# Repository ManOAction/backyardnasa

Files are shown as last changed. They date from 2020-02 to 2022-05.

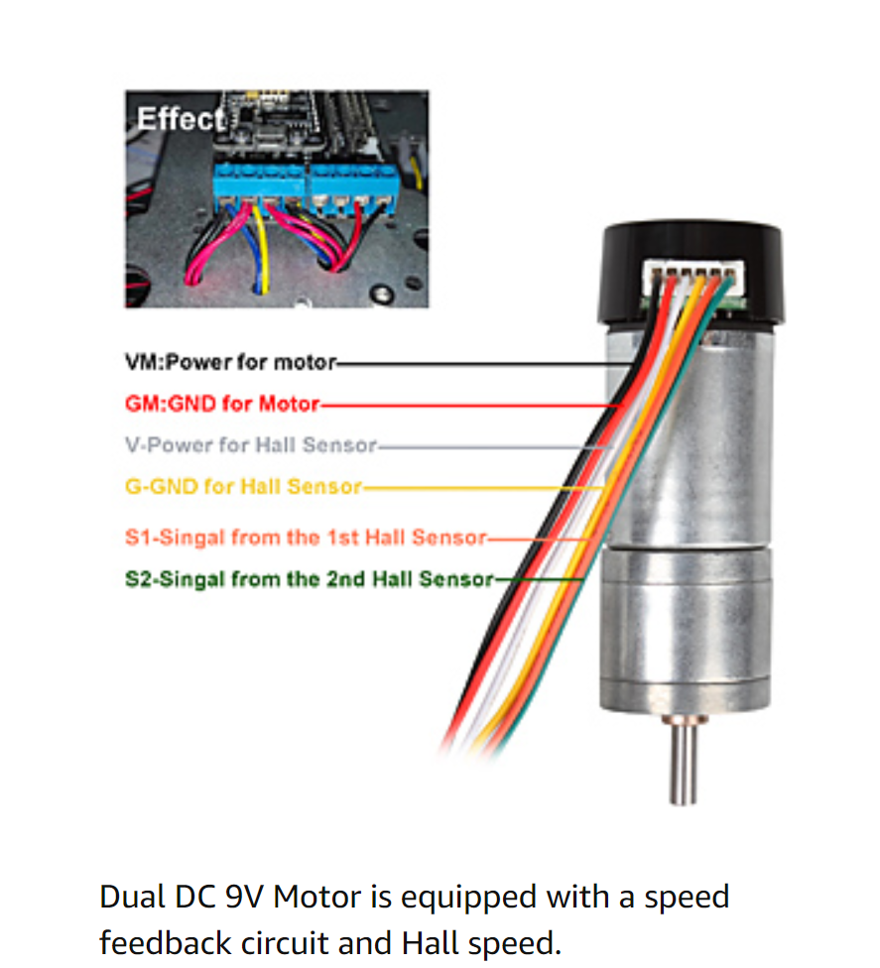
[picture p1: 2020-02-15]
docs/ChassisV2_Motor_WiringDiagram.PNG

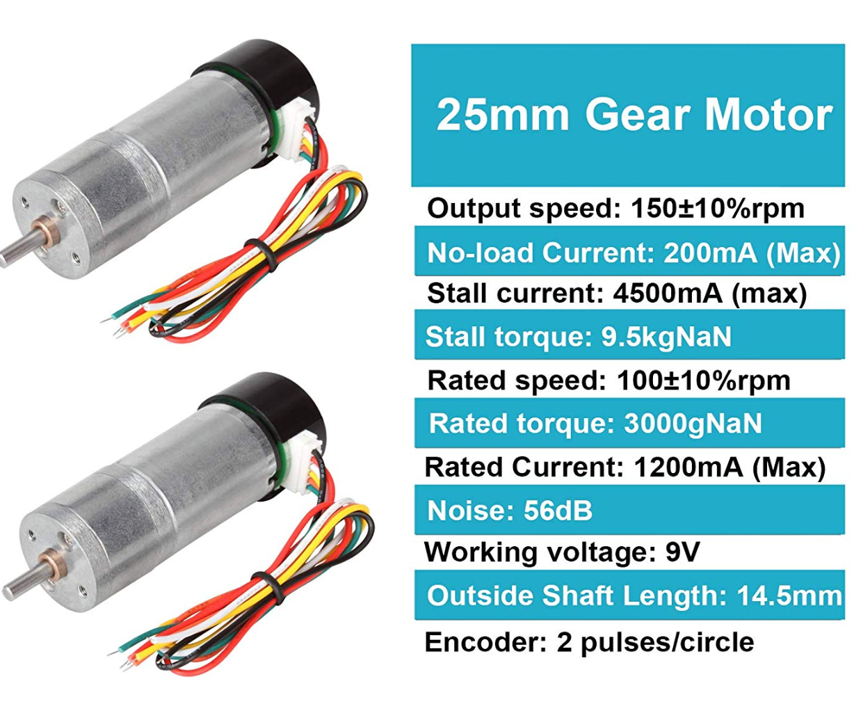
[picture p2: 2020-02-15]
docs/ChassisV2_MotorSpecs.PNG

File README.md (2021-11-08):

# Backyard NASA Rover Project
I figured making a robot rover that lived on its own somewhere and sent pictures of
rocks back to me couldn't be that hard if the gubberment folks at NASA could do it.

Her name is Matilda, and this is her story.

We started using this tutorial.
https://projects.raspberrypi.org/en/projects/physical-computing/3

New Documentation is being implemented here in Notion:
https://www.notion.so/Matilda-4c2012eff4d847c4a76360bea5a4a66a

# ChangeLog
2021-10-29, JDL -- Oh man, it's been a long time.  Moving docs to Notion and learning ROS
2020-12-27, JDL -- Updating diary and writing new roadmap for 2021
2020-07-26, JDL -- Motors, Atmo, Sonic, and Magna systems are all working.
2020-07-25, JDL -- Starting it up again.  Stuff's broke.
2020-02-22, JDL -- Rover Patterns, Temp Sensors, and Chat Capabilities
2019-11-18, JDL -- First Draft

# TODO
  Now being tracked in the "Current Roadmap Section"

# Other Ideas
Automatic Hard Iron Offset Recalibration: Use the magnet calibrator logic in the middle of
    360 turning to reset and reassign offset variables.

# Changes from Stock Raspian Setup
############################################################

We're reconfiguring the Pi to enable I2C and adding it to the kernal.
https://www.instructables.com/id/Raspberry-Pi-I2C-Python/
Note: When it says "i2cdetect -y 0" you need to say "i2c detect -y 1"

We're using an ancient library with docs listed here. (got to be something better)
http://wiki.erazor-zone.de/wiki:linux:python:smbus:doc

Following this to enable the SPI bus.
https://tutorials-raspberrypi.com/infrared-distance-measurement-with-the-raspberry-pi-sharp-gp2y0a02yk0f/

# Misc Thoughts
###########################################################

Check Bot Secrets for API info related to Chatbots

Use i2cdetect -y 1 to confirm I2C connections

Current board is loaded up on a Pi B+
pi@192.168.122.195 was the last known location
-u pi -p raspberry

##########################################################

# Broad Roadmap
##########################################################

Phase I: Basic Capabilities:
  - Pictures of Objects
  - Geofencing
  - Talking to Slack Channel  
  - Passive Charging and Voltage Checking

Phase II: Initial Backyard Trials
  - Success after multiple days of continuous operation achieved

Phase III: Scale to Pasture Size
  - Build to "coffee table" size

Phase IV: Profit?

# Current Roadmap (Newly drafted on 12/27)
##########################################################

Separate Motor Power Supply
  - This means having the computer run on a self contained system away from the
  drive motors.

  - Twin Sonic Sensors (HCSR04) for the left and right bumpers.

  - Functioning camera module that talks to a social account (slack?)

  - Update 3D printed housing for sensors, Pi, and batteries.

  - Capable of autonomous functioning until batteries deplete themselves.

# Diary
##########################################################

12/27, JDL - After lying dormant for months, matilda boots and runs fine, but the motors and power issue
  remain an issue.   I'm going to pursue using a NiMH battery to power the motors with a MOSFET in between
  to turn the battery on and off.  It looks like charging NiMH is a bit of a pain, but we're going to move
  forward with it since it's what we've got.   Passive charging/recharging may be a feature that is a long
  ways down the road.  We may as well get it to function long enough to deplete it's batteries before we try
  to learn how to recharge it.

7/26, JDL - I got tripped up on BCM/DPI pin numbering and it took a long time to fix.  Everything's working
  right now.  I'm going to clean up the codebase and then move on to a new feature to add.

7/26, JDL - This is dumb.  After looking at the official CircuitPython libraries for the HCSR04, they
  just have a poor feature set compared to this guy's custom one.  https://github.com/MarkAHeywood/Bluetin_Python_Echo
  I'm switching back to using it.

7/25, JDL - Starting back into it, and stuff's broke as we were mixed up between the Blinka library
  from Adafruit and the old stuff we had.  Frustrated because it was working until I patched a change.
  Locomotion is the only thing working and it only works at low voltage (<5V).  I need to find if I
  can use capacitors or something else to prevent the battery from shorting anytime I want more
  voltage from it.  Trying to start piece by piece putting things back online.

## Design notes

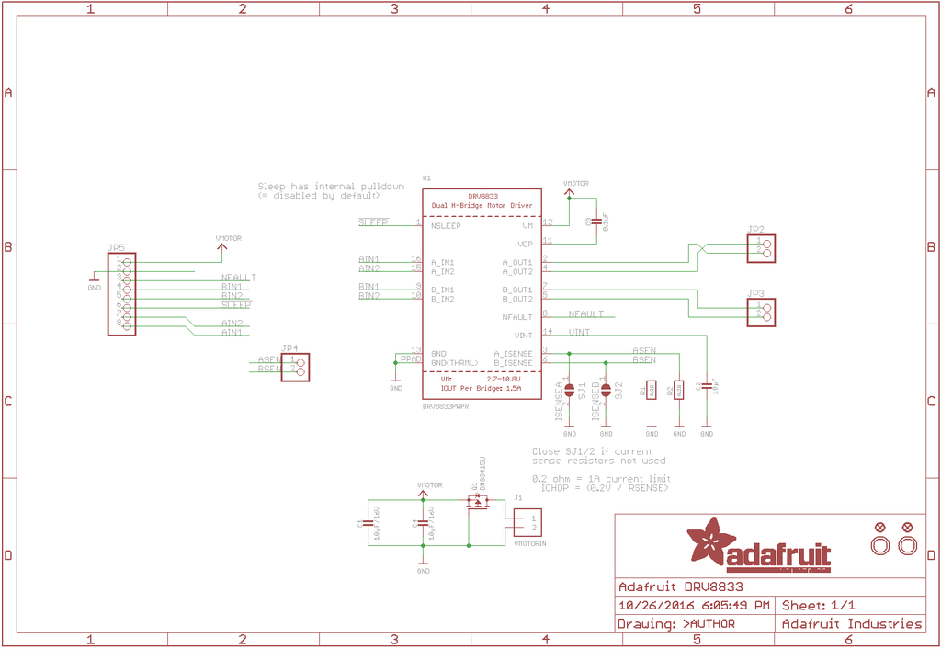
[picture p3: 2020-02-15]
docs/MotorController_Schematic.png

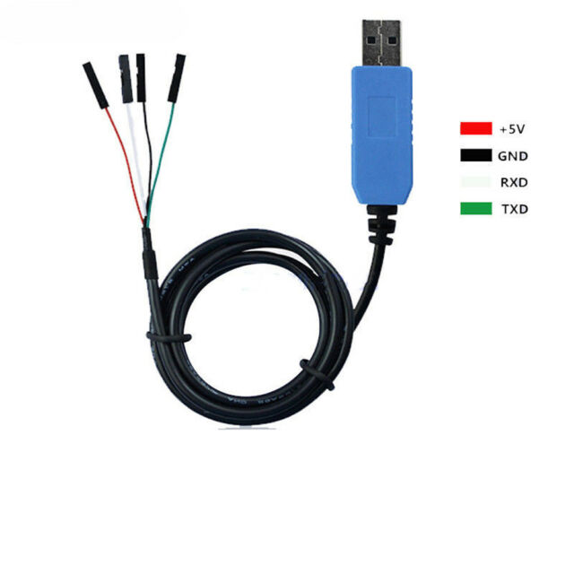
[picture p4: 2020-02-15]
docs/SerialToTTLMeaning.jpg

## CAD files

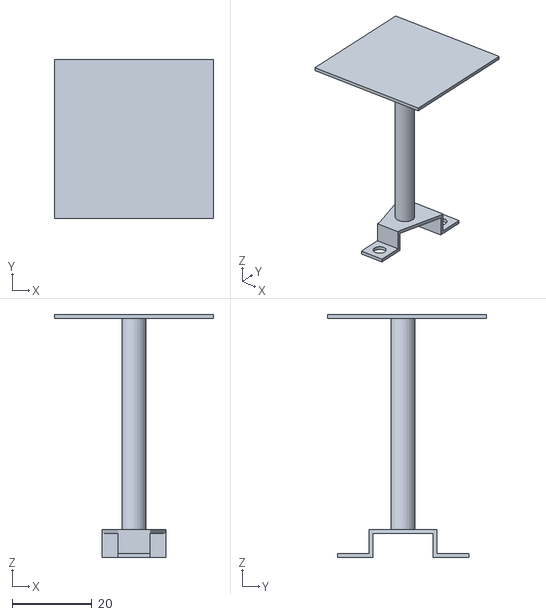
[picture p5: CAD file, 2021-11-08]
printables/CameraStand.stl
40.0 x 40.0 x 61.0

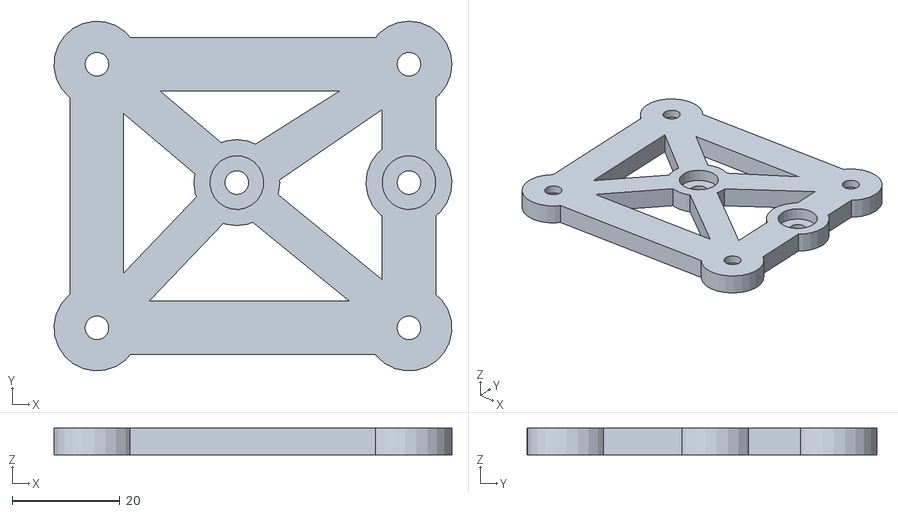
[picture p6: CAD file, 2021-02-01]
printables/PiBoard2.stl
74.0 x 65.0 x 5.00

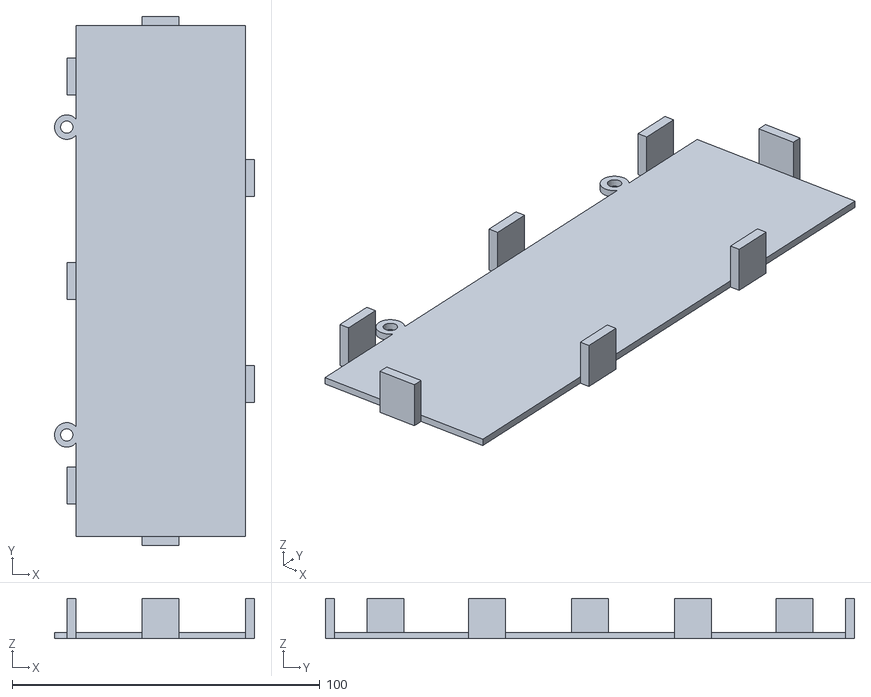
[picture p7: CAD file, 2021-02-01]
printables/Breadboard3D.stl
65.0 x 172.0 x 13.0

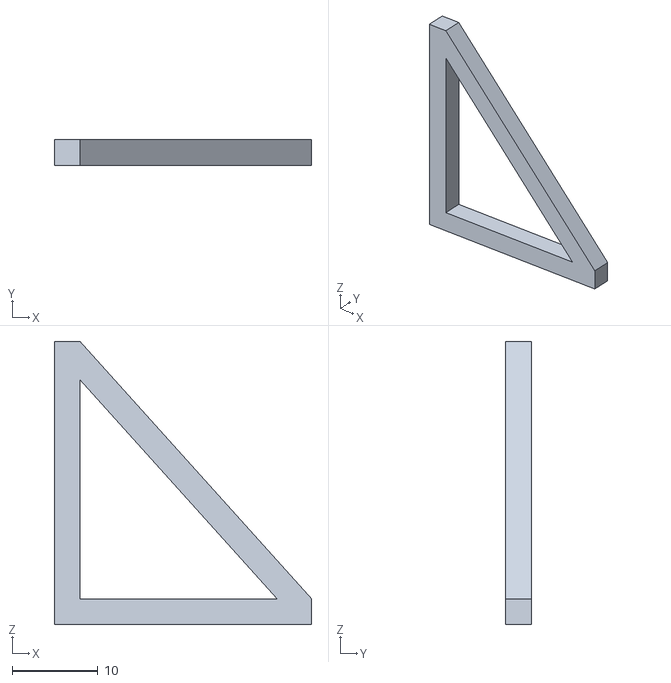
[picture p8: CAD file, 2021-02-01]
printables/AngleTest.stl
30.0 x 3.00 x 33.0

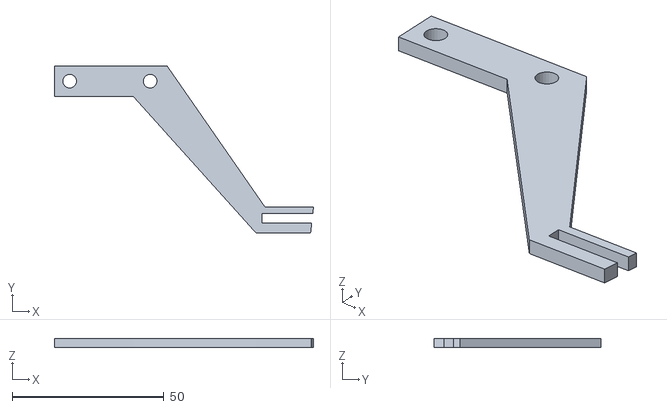
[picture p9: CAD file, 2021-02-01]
printables/SonicBracket_V2.stl
85.3 x 55.0 x 3.00

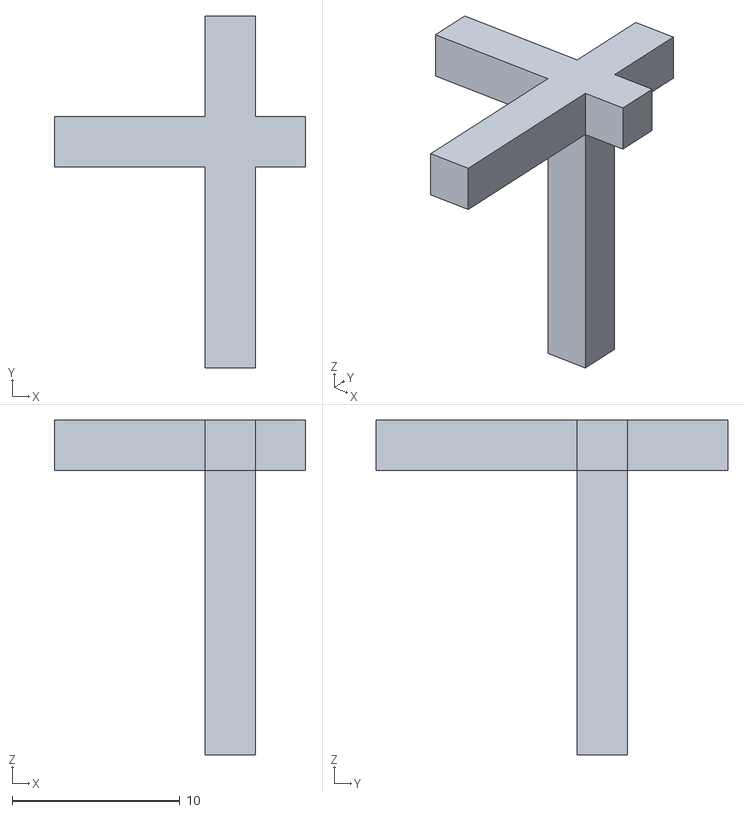
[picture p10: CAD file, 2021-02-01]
printables/SupportTest.stl
15.0 x 21.0 x 20.0

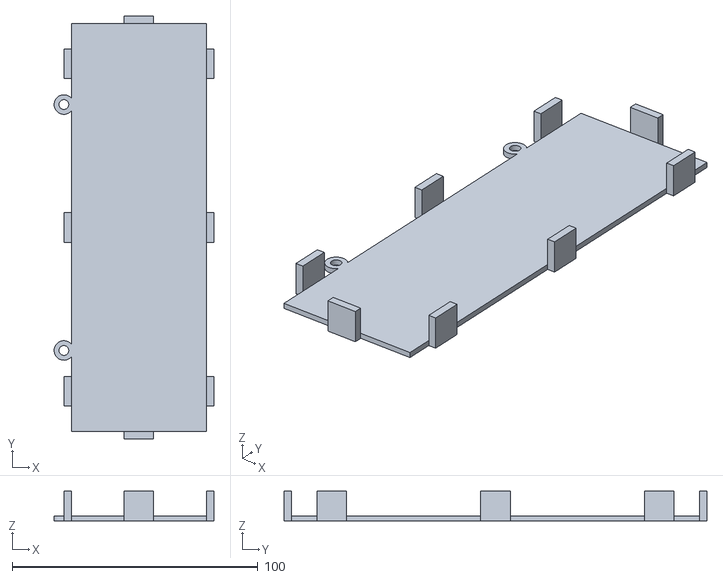
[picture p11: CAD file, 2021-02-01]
printables/Breadboard.stl
65.0 x 172.0 x 12.0

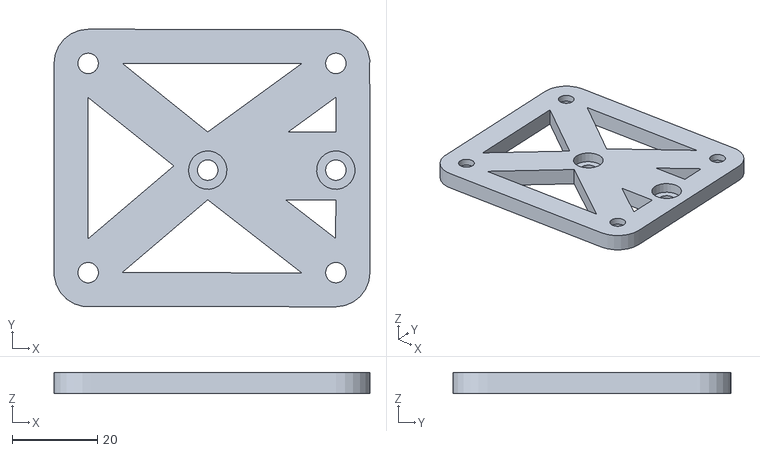
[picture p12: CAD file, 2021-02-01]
printables/PiBoard.stl
74.0 x 65.0 x 5.00

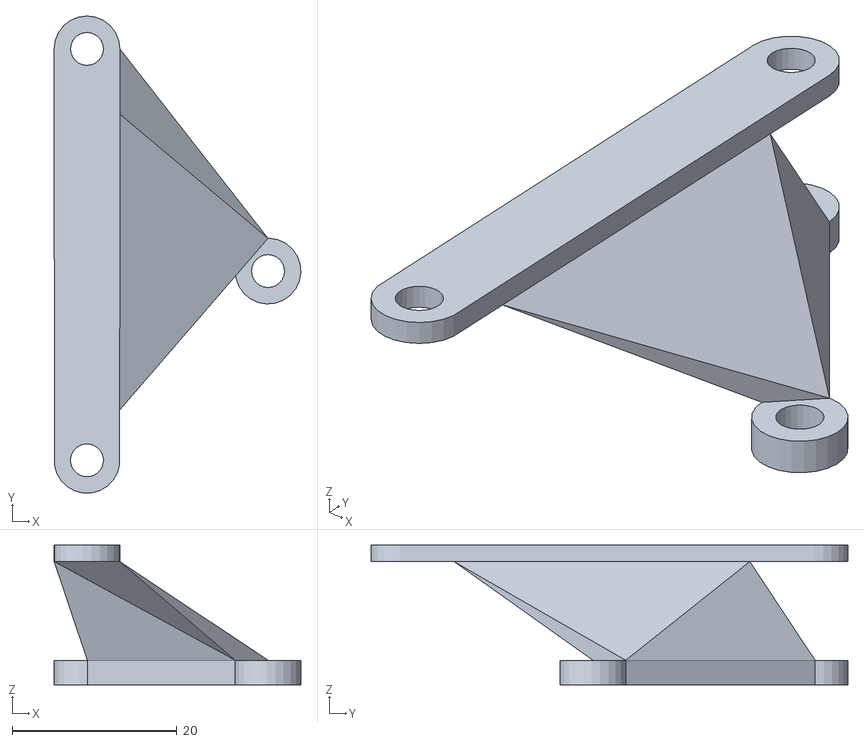
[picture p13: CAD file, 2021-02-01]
printables/PiBoard3.stl
30.0 x 58.0 x 17.0

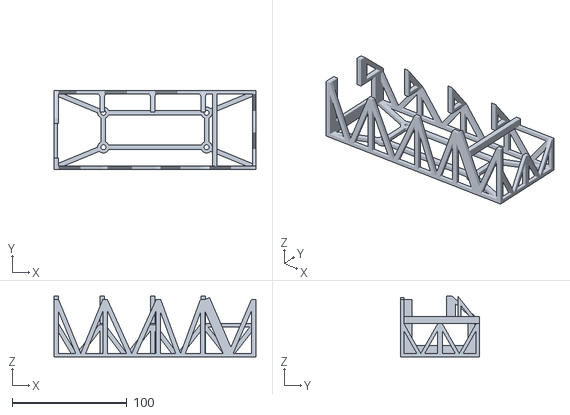
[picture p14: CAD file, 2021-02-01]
printables/BatteryBracket_V2.stl
176.0 x 69.0 x 53.0

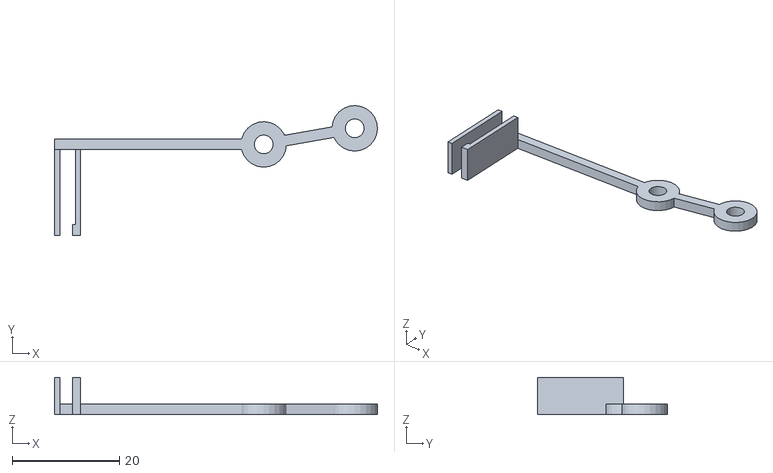
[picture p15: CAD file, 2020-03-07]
printables/sonicbracket_printable.stl
60.3 x 24.2 x 7.00

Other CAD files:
printables/AngleTest.skp
printables/BatteryBracket_V2.skp
printables/BatteryBracket_V2_baseplate.skp
printables/Breadboard.skp
printables/Breadboard3D.skp
printables/CameraStand.skp
printables/PiBoard.skp
printables/PiBoard2.skp
printables/PiBoard3.skp
printables/SonicBracket_V2.skp
printables/SupportTest.skp
printables/sonicbracket_preprint.skp
printables/sonicbracket_printable.skp

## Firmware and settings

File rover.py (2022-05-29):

"""This is the central rover behavior script.  This holds the behavior for
roving =and basic UI.

# changelog
2020-02-15, JDL: Creating stable loops and move commands
2019-11-24, JDL: First draft.


# Dependencies

Blinka Library
-------------
https://learn.adafruit.com/circuitpython-on-raspberrypi-linux/installing-circuitpython-on-raspberry-pi
sudo pip3 install adafruit-blinka -U

busio
board
adafruit_fxos8700
adafruit_fxas21002c
adafruit_si7021
------------

Bluetin Echo
------------
https://github.com/MarkAHeywood/Bluetin_Python_Echo
sudo pip3 install Bluetin_Echo -U

Bluetin_Echo
------------

"""

from gpiozero import LED, Motor
from time import sleep


# These are the Blinka tools for managing the related sensors
from busio import I2C
import board
from adafruit_fxos8700 import FXOS8700  # accelo / magnetometer
from adafruit_fxas21002c import FXAS21002C  # gyro
from adafruit_si7021 import SI7021  # temp and humidiy
from Bluetin_Echo import Echo  # HCSR04 Module Uses BCM Pins!


# Constants (move externaly to a config when you have time)
####################################################
NinetyDegreeTime = float('.65')
OneEightyDegreeTime = float('1.3')
RightTurnMod = float('1')  # float('1.109')
MotorSpeed = float('.8')

mag_offset_x = float('25')
mag_offset_y = float('-28')
mag_offset_z = float('-85')

####################################################

# Sensing
####################################################


def report_atmo():
    print("The Temperature: %0.1f F" % (AtmoSensor.temperature*(9/5)+32))
    print("Humidity: %0.1f %%" % AtmoSensor.relative_humidity)

    return True


def report_dist():
    samples = 3
    i = 0
    while i < 20:
        d = LeftEye.read('cm', samples)
        print('Left: ', d, 'cm')
        d = RightEye.read('cm', samples)
        print('Right: ', d, 'cm')
        sleep(.25)
        i += 1

    return True


# ___  ___                                    _
# |  \/  |                                   | |
# | .  . | _____   _____ _ __ ___   ___ _ __ | |_
# | |\/| |/ _ \ \ / / _ \ '_ ` _ \ / _ \ '_ \| __|
# | |  | | (_) \ V /  __/ | | | | |  __/ | | | |_
# \_|  |_/\___/ \_/ \___|_| |_| |_|\___|_| |_|\__|
#################################################


def move_forward(MoveTime):
    print('Moving forward.')
    MotorWake.on()
    RMotor.forward(MotorSpeed)
    LMotor.forward(MotorSpeed)
    sleep(MoveTime)
    RMotor.stop()
    LMotor.stop()
    MotorWake.off()
    print('End moving forward.')
    return True


def move_reverse(MoveTime):
    print('Moving backwards.')
    MotorWake.on()
    RMotor.backward(MotorSpeed)
    LMotor.backward(MotorSpeed)
    sleep(MoveTime)
    RMotor.stop()
    LMotor.stop()
    MotorWake.off()
    return True


def move_turnleft(MoveTime):
    print('Turning left.')
    MotorWake.on()
    RMotor.forward(MotorSpeed)
    LMotor.backward(MotorSpeed)
    sleep(MoveTime)
    RMotor.stop()
    LMotor.stop()
    MotorWake.off()
    return True


def move_turnright(MoveTime):
    print('Turning right.')
    MotorWake.on()
    RMotor.backward(MotorSpeed)
    LMotor.forward(MotorSpeed)
    sleep(MoveTime*RightTurnMod)
    RMotor.stop()
    LMotor.stop()
    MotorWake.off()
    return True


# Patterns
##############################################
def move_box(MoveTime):
    move_forward(MoveTime)
    move_turnleft(NinetyDegreeTime)
    move_forward(MoveTime)
    move_turnleft(NinetyDegreeTime)
    move_forward(MoveTime)
    move_turnleft(NinetyDegreeTime)
    move_forward(MoveTime)
    move_turnleft(NinetyDegreeTime)


def findpath(direction):
    
    dL = 1
    dR = 1
    while (dR == 0 or dL <= 80) and (dR == 0 or dR <= 80):
        if direction == 'left':
            move_turnleft(float(.1))
        elif direction == 'right':
            move_turnright(float(.1))
        else:
            print('Impossible directon parameter.')
            raise ValueError

        sleep(.5)
        dL = LeftEye.read('cm', 3)
        dR = RightEye.read('cm', 3)
    
    return True
            

def move_hunt():
    objectfound = 0
    dL = LeftEye.read('cm', 5)
    dR = RightEye.read('cm', 5)
    while objectfound < 100:
        MotorWake.on()
        RMotor.forward(float(MotorSpeed*.2))
        LMotor.forward(float(MotorSpeed*.2))
        print('Moving Forward...')
        dL = 0
        dR = 0

        while (dL == 0 or dL > 40) and (dR == 0 or dR > 40):
            dL = LeftEye.read('cm', 3)
            print('Left ', dL, 'cm')
            dR = RightEye.read('cm', 3)
            print('Right ', dR, 'cm')

        RMotor.stop()
        LMotor.stop()
        MotorWake.off()
        print('Object Found!')
        objectfound += 1
        sleep(.5)
        # print('Reversing...')
        # move_reverse(float(.3))
        # sleep(1)
        print('Turning...')
        print(f'Right eye distance was {dR}.')
        if (int(dR) % 2) == 0:
            print(f"""That's an even number, so I'm turning right.""")
            findpath('right')
        else:
            print(f"""That's an odd number, so I'm turning left.""")
            findpath('left')
        


# ______
# | ___ \
# | |_/ /_____   _____ _ __
# |    // _ \ \ / / _ \ '__|
# | |\ \ (_) \ V /  __/ |
# \_| \_\___/ \_/ \___|_|
#################################################
def display_options():
    print("""

    #############
    x for exit
    wasd keys for directional controls. Capital letters for custom turns.
    c for 180
    b for Box Pattern

    r for Atmospheric Report
    p for Distance Sensing Mode
    h for Hunt Mode
    #############

    """)

    return True


def rover_initialize():

    global RMotor, LMotor, MotorWake, AtmoSensor, LeftEye, RightEye, Accelo, Gyro

    # Initializing I2C for sensors
    i2c = I2C(board.SCL, board.SDA)

    # Initializing Gyro and Magnetometer
    Accelo = FXOS8700(i2c)
    Gyro = FXAS21002C(i2c)

    # Initializing Atmo Sensor
    AtmoSensor = SI7021(i2c)

    # Annoyingly it looks like the HCSR04 Libary uses DPI Pin Numbering instead
    # of Broadcom.  Check here https://pinout.xyz/pinout/pin18_gpio24
    # Read about speed of sound calibration in doc
    # BCM 23 & 24 are DPI 19 and 20
    LeftEye = Echo(23, 24)
    RightEye = Echo(17, 27)

    MotorWake = LED(17)
    MotorWake.off()

    # Args are GPIO Pins for forward, backward, and motor controller sleep
    RMotor = Motor(13, 6)  # Motor(19, 26, 13)
    LMotor = Motor(19, 26)  # Motor(20, 21, 13)

    return True


def rover_loop():

    rover_quit = False

    while rover_quit is not True:

        display_options()

        print('What is thy bidding, master?')
        user_input = input()

        try:
            # Core Commands
            ######################
            if user_input == 'x':
                return False

            if user_input == 'w':
                print('For how many seconds?')
                move_forward(float(input()))

            if user_input == 'a':
                print('90 Time is set to {0}'.format(NinetyDegreeTime))
                move_turnleft(float(NinetyDegreeTime))

            if user_input == 'A':
                print('For how many seconds?')
                move_turnleft(float(input()))

            if user_input == 's':
                print('For how many seconds?')
                move_reverse(float(input()))

            if user_input == 'd':
                move_turnright(float(NinetyDegreeTime))

            if user_input == 'D':
                print('For how many seconds?')
                move_turnright(float(input()))

            if user_input == 'c':
                print('180 Time is set to {0}'.format(OneEightyDegreeTime))
                move_turnleft(float(OneEightyDegreeTime))

            if user_input == 'b':
                print('How big a box?')
                move_box(float(input()))

            if user_input == 'r':
                report_atmo()

            if user_input == 'p':
                report_dist()

            if user_input == 'h':
                move_hunt()

        except Exception as errormessage:
            print('Problem with user input...')
            print(errormessage)

        rover_quit = False

    return True


#  _____                    _
# |  ___|                  | |
# | |____  _____  ___ _   _| |_ ___
# |  __\ \/ / _ \/ __| | | | __/ _ \
# | |___>  <  __/ (__| |_| | ||  __/
# \____/_/\_\___|\___|\__,_|\__\___|
###############################################################################

if __name__ == '__main__':
    rover_initialize()
    rover_loop()

print('I think we\'re done here.')

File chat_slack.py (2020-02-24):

import json
import requests
import re


import bot_secrets.twit_secrets as secrets






################ Post using chat api
# headers = {
#     'Authorization': 'Bearer {0}'.format(secrets.SlackToken),
#     'Content-type': 'application/json',
# }
#
# data = """{
#     "channel":"C061EG9SL",
#     "text":"Hello World, again." #,
#     # "attachments": [{"text":"Who wins the lifetime supply of chocolate?",
#     #                 "fallback":"You could be telling the computer exactly what it can do with a lifetime supply of chocolate.",
#     #                 "color":"#3AA3E3",
#     #                 "attachment_type":"default","callback_id":"select_simple_1234",
#     #                 "actions":[{"name":"winners_list","text":"Who should win?","type":"select","data_source":"users"}]}]
#     }'
# """
# response = requests.post('https://slack.com/api/chat.postMessage', headers=headers, data=data)


# ###############
# headers = {
#     'Content-type': 'application/x-www-form-urlencoded',
#     'Authorization': 'Bearer {0}'.format(secrets.SlackToken)
# }
#
# data = """{
#     "channel":"#matilda-talk",
#     "text":"Yeah, I can talk now."}
#     """
#
# response = requests.post('https://slack.com/api/chat.postMessage', headers=headers, data=data)
#
# print(response.content)
# MatildaName = re.compile('<@UTZNYQU9G>')


##############################################
def get_most_recent_message():
    headers = {
        'Content-type': 'application/x-www-form-urlencoded'
        }

    MessageText = False

    response = requests.get('https://slack.com/api/conversations.history?token={0}&channel=CUCGQMTHN&limit=15'.format(secrets.SlackToken), headers=headers)
    response = json.loads(response.content)
    # print(response)
    response = response['messages']

    for message in response:
        if re.match(r"<@UTZNYQU9G>", message['text']):
            MessageText = print(message['text'])
            return MessageText

    return MessageText


def post_to_channel(message):
    headers = {
        'Content-type': 'application/x-www-form-urlencoded',
        'Authorization': 'Bearer {0}'.format(secrets.SlackToken)
            }
    data = """{
        "channel":"#matilda-talk",
        "text":"{0}".}
        """.format(message)
    response = requests.post('https://slack.com/api/chat.postMessage', headers=headers, data=data)

    return True

##############################################


while __name__ == "__main__":
    

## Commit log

2020-02-15 Adding wiring schematics
2020-02-18 Adding motor speed variable to fix the drift in the motors.
    [rover.py]
2020-02-22 Adding a chat loop and functionality for temp sensor.
    Temp Sensor and chat now working(ish)
2020-02-23 Incorporated atmo sensor into rover
    Incorporated atmo sensor into rover.
2020-02-24 updating chatbot test
    updating chatbot test
    [matildaboard.kicad_pcb, matildaboard.sch]
2020-02-24 Update rover.py
    Added error handling for command
    [rover.py]
2020-03-02 kiCAD Files for PCB
    Adding kiCAD Files for Eventual PCB
    [matildaboard-B_Cu.gbr, matildaboard-B_Mask.gbr, matildaboard-B_Paste.gbr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]
2020-03-07 Docs and Tweaks
    Adding printable files for brackets, and converting sensor libraries to Blinka.
    [sonicbracket_preprint.skp, sonicbracket_printable.skp, sonicbracket_printable.stl]
2020-07-25 Fixing hunt, trying to unbreak Atmo Sensor.
    [rover.py]
2020-07-26 Fixed sonicsensor and hunt mode. Fixed magnometer to give a heading.
    [rover.py]
2020-12-30 Implementing camera tests, and testing VS Code git
2021-02-01 Adding all kinds of gorgeous new brackets. Body style 1.0
    [AngleTest.skp, AngleTest.stl, BatteryBracket_V2.skp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]
2022-05-28 pin fixes
